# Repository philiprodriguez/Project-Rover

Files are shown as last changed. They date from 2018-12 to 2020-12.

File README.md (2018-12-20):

# Project Rover
## Description
  Project Rover is abstractly a remotely-controllable robot with a camera for
FPV driving. It has the ability to be docked or parked into a charging spot so
that is can be driven remotely indefinitely (or, well, for the lifespan of the
physical components on the robot). The camera can be tilted up and down. It can
also be panned by simply turning the robot.

## Implementation Description
  Project Rover is developed using primarily the Android platform. The robot
contains a dedicated Android device. This Android device supplies the robot with
a camera to use, a computer on which to run the server application, a flash LED
to be used as a headlight, a Bluetooth connection, and a Wi-Fi connection. The
client sends locomotion commands to the server over a standard Java Socket. The
server process the commands and sends them off via Bluetooth to a Teensy 3.x
device, which has an attached L298N motor controller to power two drive motors.
The robot (server Android device, Teensy 3.x, motors, etc) is powered by a 12V
SLA AGM battery of 144 watt-hours, which should supply at a minimum 6 hours of
continuous, full-speed/full-power run time. To charge, the robot simply drives
into its parking spot, which has two power rails that connect with plates on the
underbelly of the robot. The server streams image data through a standard Java
Socket to the client Android application. This image data is simply a stream of
JPEG frames. Typical connection requirements are 300 KB/s. Typical image latency
is about 150-500 ms depending on if a LAN connection is used vs a remote
connection or even a cellular 4G connection.

Copyright Philip Rodriguez

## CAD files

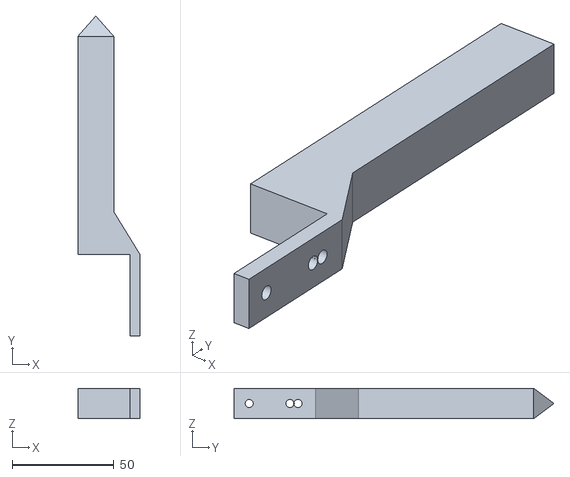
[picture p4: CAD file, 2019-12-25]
STL Files/Arm 2 v3.stl
30.7 x 157.5 x 15.0

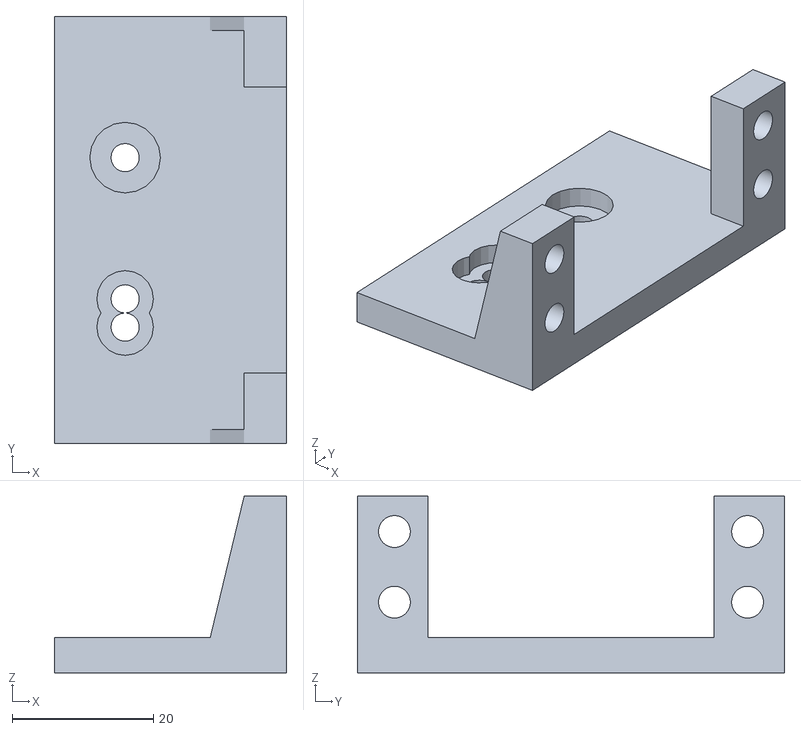
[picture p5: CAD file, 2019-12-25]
STL Files/Arm Base Angle Bracket R6.stl
32.8 x 60.5 x 25.0

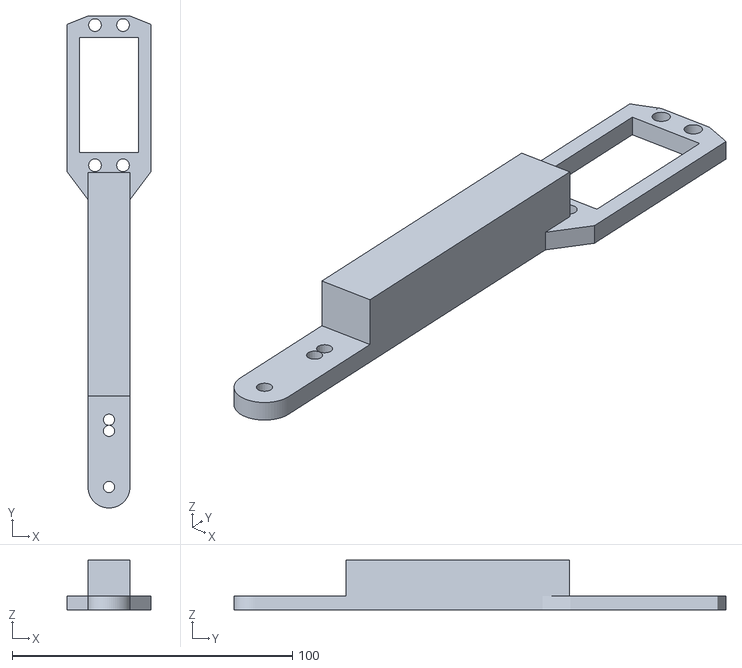
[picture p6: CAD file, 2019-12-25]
STL Files/Arm 1 R5.stl
30.0 x 175.5 x 17.7

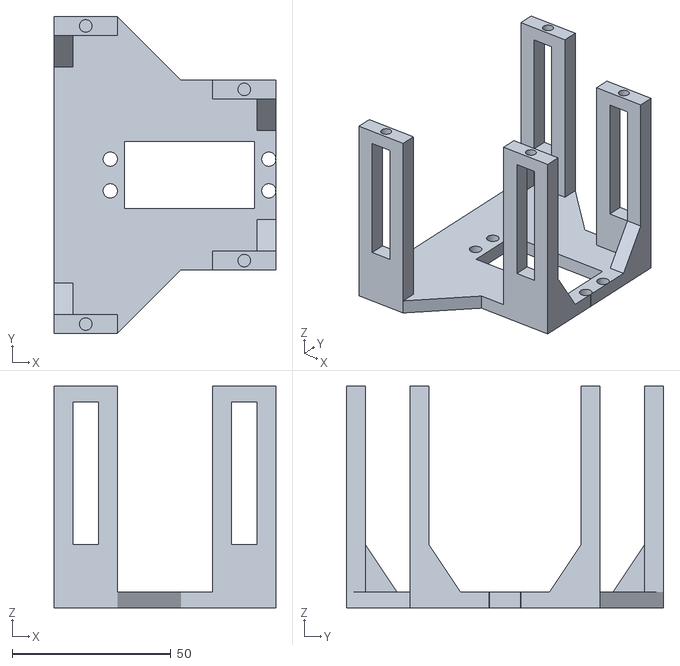
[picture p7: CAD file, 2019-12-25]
STL Files/Arm Base R4.stl
70.0 x 100.0 x 70.0

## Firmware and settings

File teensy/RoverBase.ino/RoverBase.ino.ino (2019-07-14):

/*
  Philip Rodriguez
  December 7, 2018

  This is a simple software for the Teensy that is the basic controller for the robot. This software's job is to
  take commands in over the Bluetooth Serial module on the Serial3 interface, and then "apply" those commands to
  the physical hardware of the robot, whether it be the motors, lights, servos, etc... This should be a wait-free
  and very simple code. Process incoming commands sequentially, without any delaying if at all possible.

  Update May 29, 2019

  Add ability to read battery level and send it back periodically to the Android device.

  Update July 8, 2019

  Add ability to control new robotic arm of 3 servos.
*/

#include <Servo.h>

int pinLED = 13;
int pinVoltageRead = A0;
int pinServoTilt = 16;
int pinLeftForward = 23;
int pinLeftBackward = 22;
int pinRightForward = 21;
int pinRightBackward = 20;
int pinServoArmBase = A3;
int pinServoArmOne = A4;
int pinServoArmTwo = A5;

Servo servoTilt;

Servo servoArmBase;
float servoArmBaseLastRadians = 0.0;
Servo servoArmOne;
float servoArmOneLastRadians = 0.0;
Servo servoArmTwo;
float servoArmTwoLastRadians = 0.0;

// Squish the range [0, maxRadians] radians into [544, 2400]
int convertRadianstoMicroseconds(float angle, float maxRadians) {
  float percentage = angle/maxRadians;
  int us = (int)(544.0+(1856.0*percentage));
  // Clip to prevent overdriving the servo
  us = max(544, us);
  us = min(2400, us);
  return us;
}

// Account for the zero shift amount so we can support some negative angles
// Limit range from -20 deg to 220 deg
void setServoArmBase(float thetaRadians) {
  thetaRadians = min(thetaRadians, 3.8397);
  thetaRadians = max(thetaRadians, -0.3491);
  servoArmBaseLastRadians = thetaRadians;
  servoArmBase.writeMicroseconds(convertRadianstoMicroseconds(thetaRadians+(0.5306), 4.3074));
}

void setServoArmOne(float thetaRadians) {
  thetaRadians = min(thetaRadians, 2.2689); // 130 deg
  thetaRadians = max(thetaRadians, -0.1309); // -7.5 deg
  servoArmOneLastRadians = thetaRadians;
  servoArmOne.writeMicroseconds(convertRadianstoMicroseconds(2.49582-(thetaRadians+0.1309), 4.3459));
}

void setServoArmTwo(float thetaRadians) {
  thetaRadians = min(thetaRadians, 5.218); // 299 deg
  thetaRadians = max(thetaRadians, 0.7854); // 45 deg
  servoArmTwoLastRadians = thetaRadians;
  servoArmTwo.writeMicroseconds(convertRadianstoMicroseconds(thetaRadians-0.7854, 4.4331));
}

void setup() {
  pinMode(pinLED, OUTPUT);
  
  // initialize the digital pin as an output.
  pinMode(pinLeftForward, OUTPUT); // Left forward
  pinMode(pinLeftBackward, OUTPUT); // Left backward
  pinMode(pinRightForward, OUTPUT); // Right forward
  pinMode(pinRightBackward, OUTPUT); // Right backward

  // Read battery voltage on A0
  pinMode(pinVoltageRead, INPUT);


  // Set ALL motor pins (which are sharing the same timer) from their default of a loud 488Mhz to the silent 60Khz
  analogWriteFrequency(pinLeftForward, 22000);

  // Servo initialization
  servoTilt.attach(pinServoTilt);
  servoArmBase.attach(pinServoArmBase);
  setServoArmBase(1.57079632);
  
  servoArmOne.attach(pinServoArmOne);
  setServoArmOne(2.2689);
  
  servoArmTwo.attach(pinServoArmTwo);
  setServoArmTwo(0.7853);  
  
  Serial.begin(9600);
  Serial3.begin(9600);
  Serial3.setTimeout(10000);

  // Blink a few times to show life lol
  for (int i = 0; i < 3; i++) {
    digitalWrite(pinLED, HIGH);
    delay(500);
    digitalWrite(pinLED, LOW);
    delay(500);
  }
  Serial.println(sizeof(float));
}

#define START_SEQUENCE_LENGTH 8
const int START_SEQUENCE[START_SEQUENCE_LENGTH] = {'a', '8', 'f', 'e', 'J', '2', '9', 'p'};

int nextSerial3Byte() {
  int readVal = -1;
  while ((readVal = Serial3.read()) == -1) {
    // Do nothing!
  }
  return readVal;
}

float parseFloatFromBytes(byte * bytes) {
  unsigned int temp = 0;

  temp = temp | bytes[0];
  temp = temp << 8;
  temp = temp | bytes[1];
  temp = temp << 8;
  temp = temp | bytes[2];
  temp = temp << 8;
  temp = temp | bytes[3];
  
  float result = *(float*)&temp;
  return result;
}

void printIntBits(int b) {
  for (int i = 0; i < 32; i++) {
    if ((b&(1<<(31-i))) > 0) {
      Serial.print("1");
    } else {
      Serial.print("0");
    }
  }
}

void loop() {
  // Look for start sequence
  Serial.println("Waiting for start sequence...");
  for (int i = 0; i < START_SEQUENCE_LENGTH; i++) {
    if (nextSerial3Byte() != START_SEQUENCE[i]) {
      // Failure to read start sequence! Retry!
      return;
    }
  }
  Serial.println("Got start sequence!");
  int opcode = nextSerial3Byte();
  Serial.println("Opcode:");
  Serial.println(opcode);

  if (opcode == 'm') {
    // Motor set
    Serial.println("Opcode was for motor set...");
    int leftForward = nextSerial3Byte();
    int leftBackward = nextSerial3Byte();
    int rightForward = nextSerial3Byte();
    int rightBackward = nextSerial3Byte();
    analogWrite(pinLeftForward, leftForward);
    analogWrite(pinLeftBackward, leftBackward);
    analogWrite(pinRightForward, rightForward);
    analogWrite(pinRightBackward, rightBackward);
    Serial.println("Motors set:");
    Serial.println(leftForward);
    Serial.println(leftBackward);
    Serial.println(rightForward);
    Serial.println(rightBackward);
  } else if (opcode == 'l') {
    // LED set
    Serial.println("Opcode was for led set...");
    int val = nextSerial3Byte();
    if (val == 'h') {
      digitalWrite(pinLED, HIGH);
    } else if (val == 'l') {
      digitalWrite(pinLED, LOW);
    }
  } else if (opcode == 's') {
    // Servo set
    Serial.println("Opcode was for servo set...");
    int val = nextSerial3Byte();
    if (val >= 5 && val <= 175) {
      int curValue = servoTilt.read();
      int delayAmt = 105;
      while(curValue != val) {
        if (val > curValue) {
          curValue++;
        }
        else {
          curValue--;
        }
        servoTilt.write(curValue);
        delay(delayAmt);
        if (delayAmt > 5) {
          delayAmt-=5;
        }
      }
      // Small back off to prevent stress
      delay(200);
      if (curValue > 90) {
        servoTilt.write(curValue-4);
      } else {
        servoTilt.write(curValue+4);
      }
    }
  } else if (opcode == 'v') {
    // Voltage read
    //Serial.println("Opcode was for voltage read...");
    int voltageValue = analogRead(pinVoltageRead);
    //Serial.println("Voltage value int is:");
    //Serial.println(voltageValue);
    byte buf[START_SEQUENCE_LENGTH+1+4];
    int i;
    for (i = 0; i < START_SEQUENCE_LENGTH; i++) {
      buf[i] = START_SEQUENCE[i];
    }
    buf[i++] = 'v';
    buf[i++] = (voltageValue >> 24) & 255;
    buf[i++] = (voltageValue >> 16) & 255;
    buf[i++] = (voltageValue >> 8)  & 255;
    buf[i++] = voltageValue & 255;
    //Serial.print("Sending int bytes: ");
    for (int j = 0; j < START_SEQUENCE_LENGTH+1+4; j++) {
      //Serial.print(buf[j]);
      //Serial.print(" ");
    }
    //Serial.println();
    Serial3.write(buf, sizeof(buf));
  } else if (opcode == 'a') {
    // Arm set
    Serial.println("Opcode was for arm set...");
    byte bufBase[4];
    for (int i = 0; i < 4; i++) {
      bufBase[i] = nextSerial3Byte();
    }
    byte bufOne[4];
    for (int i = 0; i < 4; i++) {
      bufOne[i] = nextSerial3Byte();
    }
    byte bufTwo[4];
    for (int i = 0; i < 4; i++) {
      bufTwo[i] = nextSerial3Byte();
    }
    float baseRad = parseFloatFromBytes(bufBase);
    float oneRad = parseFloatFromBytes(bufOne);
    float twoRad = parseFloatFromBytes(bufTwo);
    Serial.print("Base Radians: ");
    Serial.print(baseRad);
    Serial.print(", One Radians: ");
    Serial.print(oneRad);
    Serial.print(", Two Radians: ");
    Serial.print(twoRad);
    Serial.println();
    setServoArmBase(baseRad);
    setServoArmOne(oneRad);
    setServoArmTwo(twoRad);
  } else {
    Serial.println("Illegal opcode!");
    return;
  }
}

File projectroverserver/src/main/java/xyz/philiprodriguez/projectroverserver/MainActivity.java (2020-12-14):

package xyz.philiprodriguez.projectroverserver;

import android.Manifest;
import android.content.pm.PackageManager;
import android.graphics.SurfaceTexture;
import android.hardware.camera2.CameraAccessException;
import android.hardware.camera2.CameraCaptureSession;
import android.hardware.camera2.CameraCharacteristics;
import android.hardware.camera2.CameraDevice;
import android.hardware.camera2.CameraManager;
import android.hardware.camera2.CaptureRequest;
import android.hardware.camera2.params.StreamConfigurationMap;
import android.media.AudioFormat;
import android.media.AudioManager;
import android.media.AudioRecord;
import android.media.AudioTrack;
import android.media.MediaRecorder;
import android.media.audiofx.LoudnessEnhancer;
import android.media.audiofx.NoiseSuppressor;
import android.net.wifi.WifiManager;
import android.os.BatteryManager;
import android.os.Handler;
import android.os.HandlerThread;
import android.support.annotation.NonNull;
import android.support.v4.content.ContextCompat;
import android.support.v7.app.AppCompatActivity;
import android.os.Bundle;
import android.text.format.Formatter;
import android.util.Size;
import android.view.Surface;
import android.view.TextureView;
import android.view.View;
import android.widget.Button;
import android.widget.ScrollView;
import android.widget.TextView;

import java.nio.ByteBuffer;
import java.util.ArrayList;
import java.util.Arrays;
import java.util.Collections;
import java.util.Date;
import java.util.LinkedList;
import java.util.List;
import java.util.Queue;
import java.util.concurrent.ConcurrentLinkedQueue;

import xyz.philiprodriguez.projectrovercommunications.ArmPositionMessage;
import xyz.philiprodriguez.projectrovercommunications.GlobalLogger;
import xyz.philiprodriguez.projectrovercommunications.MotorStateMessage;
import xyz.philiprodriguez.projectrovercommunications.OnArmPositionMessageReceivedListener;
import xyz.philiprodriguez.projectrovercommunications.OnLoggableEventListener;
import xyz.philiprodriguez.projectrovercommunications.OnMotorStateMessageReceivedListener;
import xyz.philiprodriguez.projectrovercommunications.OnPCMFrameMessageReceivedListener;
import xyz.philiprodriguez.projectrovercommunications.OnServerSettingsMessageReceivedListener;
import xyz.philiprodriguez.projectrovercommunications.PCMFrameMessage;
import xyz.philiprodriguez.projectrovercommunications.ProjectRoverServer;
import xyz.philiprodriguez.projectrovercommunications.ServerSettings;
import xyz.philiprodriguez.projectrovercommunications.ServerSettingsMessage;
import xyz.philiprodriguez.projectrovercommunications.ServerStateMessage;

public class MainActivity extends AppCompatActivity {
    public static final String CLASS_IDENTIFIER = "MainActivity (Server)";
    private static final int PERMISSIONS_REQUEST_CODE = 315736;
    private static final int MAX_STATUS_TEXT_SIZE = 100;

    private ProjectRoverServer projectRoverServer;

    private final LinkedList<String> statusTexts = new LinkedList<String>();

    private ScrollView scrStatusScrollView;
    private TextView txtStatusMessage;
    private Button btnStopServer;
    private TextureView txvCameraPreview;

    // Bluetooth
    BluetoothHandler bluetoothHandler;

    // Camera shit only
    CameraManager cameraManager;
    String cameraRearId;
    Size cameraSize;
    HandlerThread cameraHandlerThread;
    Handler cameraBackgroundHandler;
    CameraDevice.StateCallback cameraStateCallback;
    CameraDevice cameraDevice;
    CaptureRequest.Builder captureRequestBuilder;
    CameraCaptureSession cameraCaptureSession;

    // Camera timer only
    Handler cameraTimerHandler;
    Runnable cameraTimerRunnable;

    // Audio stuff for recording and sending to client
    AudioRecord audioRecord;
    Handler audioRecordHandler;
    HandlerThread audioRecordHandlerThread;
    Runnable audioRecordRunnable;

    // Audio stuff for playback of audio from the client
    final Queue<Short> audioPlaybackPcmValueQueue = new ConcurrentLinkedQueue<>();
    Handler audioPlaybackHandler;
    HandlerThread audioPlaybackHandlerThread;
    Runnable audioPlaybackRunnable;
    AudioTrack audioPlaybackTrack;

    // State send timer only
    Handler stateSendTimerHandler;
    Runnable stateSendTimerRunnble;

    private void setStatusAndLog(String message) {
        synchronized (statusTexts) {
            GlobalLogger.log(CLASS_IDENTIFIER, GlobalLogger.INFO, "Status: " + message);
            statusTexts.add(new Date().toString() + ": " + message);
            while (statusTexts.size() > MAX_STATUS_TEXT_SIZE) {
                statusTexts.removeFirst();
            }
            final StringBuffer sb = new StringBuffer();
            for (String s : statusTexts) {
                sb.append(s);
                sb.append(System.lineSeparator());
            }
            runOnUiThread(new Runnable() {
                @Override
                public void run() {
                    txtStatusMessage.setText(sb);
                    scrStatusScrollView.post(new Runnable() {
                        @Override
                        public void run() {
                            scrStatusScrollView.fullScroll(View.FOCUS_DOWN);
                        }
                    });
                }
            });
        }
    }

    @Override
    protected void onCreate(Bundle savedInstanceState) {
        super.onCreate(savedInstanceState);
        setContentView(R.layout.activity_main);
        initComponents();
    }

    @Override
    public void onRequestPermissionsResult(int requestCode, @NonNull String[] permissions, @NonNull int[] grantResults) {
        if (requestCode == PERMISSIONS_REQUEST_CODE) {
            boolean allGranted = true;
            for (int i = 0; i < permissions.length; i++) {
                if (grantResults[i] != PackageManager.PERMISSION_GRANTED) {
                    setStatusAndLog("The required permission " + permissions[i] + " was rejected, so the app will not resume. Restart the app to try again.");
                    allGranted = false;
                }
            }
            if (allGranted) {
                setStatusAndLog("All required permissions were granted! Resuming...");
                performOnResumeDuties();
            }
        }
    }

    private void initComponents() {
        scrStatusScrollView = findViewById(R.id.scrStatusScrollView_Main);
        txtStatusMessage = findViewById(R.id.txtStatusMessage_Main);
        btnStopServer = findViewById(R.id.btnStopServer_Main);
        txvCameraPreview = findViewById(R.id.txvCameraPreview_Main);

        btnStopServer.setOnClickListener(new View.OnClickListener() {
            @Override
            public void onClick(View v) {
                if (projectRoverServer == null || projectRoverServer.isKilled()) {
                    startServer();
                } else {
                    stopServer();
                }
            }
        });
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

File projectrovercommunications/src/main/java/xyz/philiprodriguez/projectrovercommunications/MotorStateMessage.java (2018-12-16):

package xyz.philiprodriguez.projectrovercommunications;

import java.nio.ByteBuffer;

public class MotorStateMessage implements ByteableMessage<MotorStateMessage> {

    private final long timestamp;
    private final int leftForward;
    private final int leftBackward;
    private final int rightForward;
    private final int rightBackward;

    public MotorStateMessage() {
        this(-1, -1, -1, -1, -1);
    }

    public MotorStateMessage(long timestamp, int leftForward, int leftBackward, int rightForward, int rightBackward) {
        this.timestamp = timestamp;
        this.leftForward = leftForward;
        this.leftBackward = leftBackward;
        this.rightForward = rightForward;
        this.rightBackward = rightBackward;
    }

    public int getLeftBackward() {
        return leftBackward;
    }

    public int getLeftForward() {
        return leftForward;
    }

    public int getRightBackward() {
        return rightBackward;
    }

    public int getRightForward() {
        return rightForward;
    }

    @Override
    public byte[] getBytes() {
        int extraLength = 8 + 4*4;

        ByteBuffer byteBuffer = ByteBuffer.allocate(ReceiverThread.START_SEQUENCE.length + 1 + 4 + extraLength);

        // Start sequence
        for (int i = 0; i < ReceiverThread.START_SEQUENCE.length; i++) {
            byteBuffer.put(ReceiverThread.START_SEQUENCE[i]);
        }

        // Start code
        byteBuffer.put(getStartCode());

        // Message length
        byteBuffer.putInt(extraLength);

        // timestamp
        byteBuffer.putLong(getTimestamp());

        // Bytes
        byteBuffer.putInt(leftForward);
        byteBuffer.putInt(leftBackward);
        byteBuffer.putInt(rightForward);
        byteBuffer.putInt(rightBackward);


        return byteBuffer.array();
    }

    @Override
    public MotorStateMessage fromBytes(byte[] messageBytes) {
        ByteBuffer byteBuffer = ByteBuffer.wrap(messageBytes);
        long timestamp = byteBuffer.getLong();
        int lf = byteBuffer.getInt();
        int lb = byteBuffer.getInt();
        int rf = byteBuffer.getInt();
        int rb = byteBuffer.getInt();
        return new MotorStateMessage(timestamp, lf, lb, rf, rb);
    }

    @Override
    public byte getStartCode() {
        return 10;
    }

    @Override
    public long getTimestamp() {
        return timestamp;
    }

    @Override
    public String toString() {
        return getLeftForward() + ", " + getLeftBackward() + ", " + getRightForward() + ", " + getRightBackward();
    }
}

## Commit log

2018-12-15 Added support for changing JPEG quality remotely and turning the remote device's flash on or off remotely and viewing the remote device's battery percentage remotely. Some UI updates to client connec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
2018-12-16 Refactor everything so that client and server don't need to duplicate sending and receiving thread code
2018-12-20 Updated motor PWM frequency to make it quieter
2018-12-22 Initial camera tilt support
2019-01-02 Updated Teensy code to adjust servo more carefully (slowly) to reduce stress to servo coupling point
2019-05-30 Update to support voltage sensor
2019-05-30 Update mapping from voltage value to percentage based on regression from internet charge chart
2019-06-17 Updated SenderThread so that it has two queues, one for messages that strictly must be sent eventually and one for less important droppable messages (aka, JPEG frames). This should allow for less lag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
2019-06-18 Update primary battery level logic to max out at 100% and perceive mildly higher battery level.
2019-07-11 Significantly refactor the server's MainActivity by pulling out the Bluetooth code into a separate class with proper event handling structures. Also added an untested message type for the arm positio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
2019-07-14 Significant additions to client and server to support the addition of the three-servo robotic arm poker. ArmDriver class is largely responsible for conversion from 3D coordinate to three thetas for t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
2019-07-15 Updated z-axis slider so that it spans from 0.30 to -0.15
2019-07-15 Fixed issue of TrackpadView aspect ratio not being respected by ConstraintLayout. Wrapping TrackpadViews in LinearLayout ws the fix. Not sure why ConstraintLayout refused to respect the clearly corre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
    [ConnectedActivity.java]
2019-07-24 Updated the ArmDriver so that it will directly solve for thetaB instead of performing a ternary search for it, which speeds up the algorithm by a factor of searchIterations (e.g. 5-30 times faster in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
    [MainActivity.java]
2019-07-24 Fix minor bug that would allow for thetaOne to be computed as smaller than thetaOneMin. Specifically, the bug was that splitTheta may be below thetaOneMin, and thus the ternary search, in some such c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
2019-12-25 Add client-side trim support
    [Arm 1 R5.stl, Arm 2 v3.stl, Arm Base Angle Bracket R6.stl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]
2020-12-13 First working audio link. Currently only allows clients to listen to audio at the server. Client cannot send audio to the server yet. Also, some mild code cleanup, and important gitignore updates to 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
2020-12-13 First working half-duplex bi-directional audio communication (e.g. client has a push-to-talk button that mutes the server, only superficially... to prevent feedback over the internet...)!
    [ConnectedActivity.java, MainActivity.java]
2020-12-14 Minor refactoring. Fix issue causing crash when appropriate camera size was not available.
    [ConnectedActivity.java, MainActivity.java]
2020-12-14 Switch audio from 8-bit PCM to 16-bit PCM which seems to have had a DRASTIC improvement for audio quality
